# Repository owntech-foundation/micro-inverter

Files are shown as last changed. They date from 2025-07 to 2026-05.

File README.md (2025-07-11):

# An open-source - community built micro-inverter

## Manifesto 

The project goal are : 

- Having the first open source PV micro-inverter
- Finally a design easy to repair that is no longer a black box
- Redeem your data sovereignty, you will no longer depend on a proprietary cloud to follow your solar production and consumption. 

## Open, for everyone, forever

- This project is propulsed by its community. 
- The collective work generated is meant to remain open.
- Design files are made with open source software - Namely kiCAD.

In that sense, the owntech foundation aims at protecting this technical common.

## (ultra) Preliminary specifications

- 230V AC grid code compliant
- 450W max per module
- no invasive potting that prevents reparability

## Licence 

This project is licenced under **CERN-OHL-V2-S** open source hardware licence. Licence file can be found under `License/cern-ohl-v2-s`.

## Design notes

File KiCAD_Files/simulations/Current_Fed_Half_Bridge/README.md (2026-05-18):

# LTspice Current-Fed Half-Bridge Simulation

This directory contains an LTspice simulation for a current-fed half-bridge converter stage. The schematic models the MOSFET bridge drive, input current-feed network, transformer/coupled inductors, rectifier/output stage, and a TI UCC27282 half-bridge gate driver model.

## Files

- `Current_Fed_Half_Bridge.asc` - main LTspice schematic.
- `UCC27282.asy` - custom LTspice symbol for the UCC27282 gate driver.
- `ucc27282.lib` - TI transient SPICE model for the UCC27282.

## Simulation Setup

The schematic includes these simulation directives:

```spice
.param Tsw={1/Fsw} Ton={duty*Tsw} Toff={TSw-Ton-2*dt} dt=100n duty=0.45 Fsw=200k
.tran 0 0.002 0 0.000001
K1 L1 L2 1
```

Nominal operating parameters:

- Switching frequency: `Fsw = 200 kHz`
- Duty cycle: `duty = 0.45`
- Dead time: `dt = 100 ns`
- Transient duration: `2 ms`
- Maximum timestep: `1 us`
- Input source: `Vin = 40 V`
- Gate-drive supply: `VDD = 12 V`

## Main Circuit Elements

- `U1` - UCC27282 high/low-side gate driver.
- `M1`, `M2`, `M3` - `IPP048N12N3` MOSFETs.
- `L3` and `C7` - input current-feed/filter elements.
- `L1` and `L2` - coupled inductors/transformer winding pair.
- `D1`, `D2`, `C4`, `C6`, and `R9` - rectifier, output capacitance, and load.
- `V2`, `V3` - complementary gate-drive pulse sources for `LI` and `HI`.

## Running the Simulation

1. Open `Current_Fed_Half_Bridge.asc` in LTspice.
2. Keep `UCC27282.asy` and `ucc27282.lib` available in the same project directory, or install the symbol/model into your LTspice symbol and library search paths.
3. Run the transient simulation.
4. Probe the relevant nets listed below.

If LTspice cannot find the UCC27282 symbol, update the symbol reference in the schematic or copy `UCC27282.asy` into the expected LTspice symbol path. The schematic currently references the driver symbol as `lib\\JAL\\UCC27282`.

## Useful Probe Nodes

- `Vin` - converter input voltage.
- `LI`, `HI` - gate-driver logic inputs.
- `LO`, `HO` - low-side and high-side gate-driver outputs.
- `VSH` - high-side switch node.
- `VGSH` - measured high-side gate-to-source voltage.
- `VHigh` - high-side supply node.
- `Vout` - output voltage node.
- `GNDhigh` - output-side return.
- `VOUT_mes` - behavioral output voltage measurement, `V(Vout)-V(GNDhigh)`.
- `vr1` - behavioral measurement of `V(vsh)-V(vshcap)`.
- `vr2` - behavioral measurement of `V(vsecd)-V(vsecc)`.

## Notes

- The UCC27282 model is a TI PSPICE transient model released by Texas Instruments in 2018 and included here as `ucc27282.lib`.
- The schematic depends on LTspice device models for parts such as `IPP048N12N3`, `VS-E5TX1506`, and `VS-E5TH1506`. If those models are not available in your LTspice installation, add the required vendor libraries or replace the parts with available equivalents.
- The schematic uses micro-unit values that may appear as special characters in the raw `.asc` text. LTspice should display these values normally when the schematic is opened.

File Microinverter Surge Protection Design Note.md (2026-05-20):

Surge Protection for the OwnTech microinverter

Author: Stevie Wray – Fairflow Energy Ltd.

Date: 14/05/2026

Revision: V1.0

# Rationale – Why should there be surge protection?

The microinverter is intended to be connected directly to an AC grid.
This grid could have transient over voltages from lightning, grid
switching and inductive faults. These could exceed insulation limits and
cause immediate or long term damage to sensitive components. By
including surge protection, the more sensitive components can continue
to work in a wider range of circumstances.

There is also a regulatory element where withstanding surges are a
requirements for passing EMC tests.

The relevant standards for this are:

EN 62109-1: Safety of power converters for use in photovoltaic power
systems - Part 1: General requirements

EN 62109-2: Safety of power converters for use in photovoltaic power
systems - Part 2: Particular requirements for inverters

EN 61000-4-5: Electromagnetic compatibility (EMC) – Part 4-5: Testing
and measurement techniques – Surge immunity test

# What have we done?

1\. Included an AC side Metal Oxide Varistor (MOV) and Gas Discharge
Tube (GDT) combination to protect against line to earth surges. (Live or
Neutral counting as a line) – RV1, RV3, GD1

2\. Included an AC side MOV to protect against Live to Neutral surges. -
RV2

3\. Included a further set of line to earth and live to neutral MOVs on
the converter side of the K1 grid connection relay. This set of MOVs are
paired with fuses in case of protective device failure. – RV101, RV102,
RV103, F1, F101.

4\. Considered insulation co-ordination to ensure that insulation is
sufficient in each part of the inverter.

NOTE: If a protective device fails, the microinverter will need
maintenance to replace those components.

An excerpt of the microinverter schematic is included below showing
these MOVs.

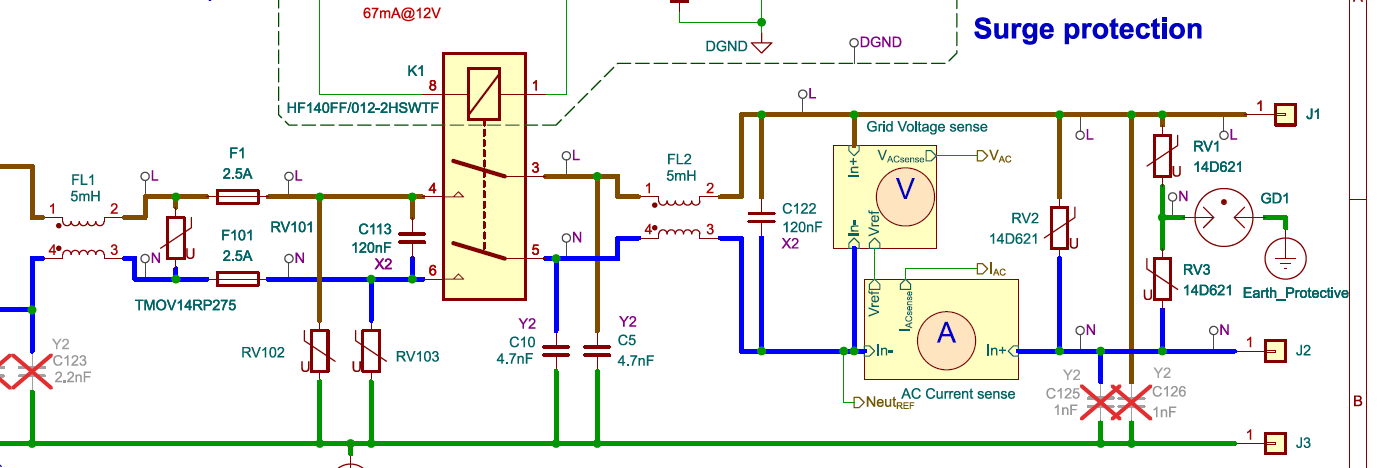
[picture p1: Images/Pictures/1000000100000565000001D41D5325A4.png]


## 

# Why have we done it that way?

On the specific device configuration, a major consideration is the
failure mode of the MOVs and the GDTs themselves. If the fault through a
GDT does not clear (reduce current to zero) then the GDT will eventually
catch fire. This is undesirable! As such, the arrangement for line to
earth fault with a MOV in series with a GDT overcomes this. Especially
if the MOV has an internal thermal fuse. The MOVs selected do have an
internal fuse.

There is also a cascade of MOV values starting with the higher values
near the AC connection to the grid, and reducing closer to the internals
of the inverter. The intent here is to ensure that sensitive components,
such as the GaN switches are protected to voltages that they can
withstand.

There is a known limitation with this current design, in that the rating
of the MOVs is still insufficient to reduce an arbitrary pulse to below
the voltage rating of the GaN switches. This is an unlikely event, as
the standard pulse simulated in this document are already a harsh
condition.

With this in mind, the intent is to meet EN61000-4-5 Surge Test Levels
as below, assuming that the AC power port is a class 4, but then
elements within the microinverter are then reduced in class.

This assumes that the standard tests are sufficient for a robust
product. From assessing them, they do seem good enough for the
microinverter’s purposes.

Essentially, the requirements we are aiming to meet are that after the
surge test (4 kV, 2 Ohm source impedance 8/20 µs pulse), the inverter
must:

- Continue to operate as intended (no degradation in performance).
- Not become unsafe (no fire, electric shock, or mechanical hazards).
- Not trip protective devices (e.g., circuit breakers) unless it is part
  of the intended safety function.

The defined voltage levels are found in this table here:

<table>
<tbody>
<tr>
<td colspan="4">Electrical Surge Test Levels (IEC/EN 61000-4-5)</td>
</tr>
<tr>
<td>Class</td>
<td>Test Level<br />
(V)</td>
<td>Max Peak Current @ 2 Ω<br />
(A)</td>
<td></td>
</tr>
<tr>
<td>1</td>
<td>500</td>
<td>250</td>
<td></td>
</tr>
<tr>
<td>2</td>
<td>1000</td>
<td>500</td>
<td></td>
</tr>
<tr>
<td>3</td>
<td>2000</td>
<td>1000</td>
<td></td>
</tr>
<tr>
<td>4</td>
<td>4000</td>
<td>2000</td>
<td></td>
</tr>
<tr>
<td>X</td>
<td>Special</td>
<td>Special</td>
<td></td>
</tr>
<tr>
<td colspan="3">X can be any level specified in product specific
standards.<br />
It can be above, below or between the others.</td>
<td></td>
</tr>
</tbody>
</table>

Wikipedia (<https://en.wikipedia.org/wiki/IEC_61000-4-5>)

Practically, the surge immunity testing is done with a combination
waveform generator, aiming to generate a 8/20 µs current pulse. Note the
waveform times refer to rise time and impulse width. Shown nicely in
this excerpt from the Brightking 621KN14 datasheet.

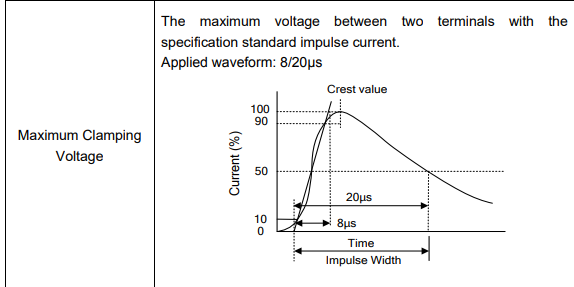
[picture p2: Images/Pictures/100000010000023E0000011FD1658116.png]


A combination waveform generator can be represented as a set of simple
circuit components, especially for simulation. The following is from a
guide found here:
<https://youspice.com/spice-simulation-of-a-combo-wave-generator/>

[](https://youspice.com/spice-simulation-of-a-combo-wave-generator/)

Cc=7.76μF, Rs1=14.8 Ohm, Rm=1.05 Ohm, Lr=9.74μH, Rs2=23.3 Ohm. The peak
voltage on Rs2 can be 1KV, 2KV,..6KV.

A SIMBA model has been produced with these parameters, pre-charging the
capacitor Cc to the desired voltage rating for the test. In this case it
is generally 4 kV.

# Simulations for verification

## RV1, RV2, RV3: Brightking 621KN14

The device selected for RV1, RV2 and RV3 is the Brightking 621KN14. The
section below shows the expected characteristics of this device, and
shows an example of it under a 4 kV, 2 Ohm input impedance surge
immunity test using a simulated combination wave generator.

Varistor voltage is the voltage
between two terminals with specified measuring current of 1mA DC.



~0 Amps at less than 620 V

~ 1 mA at 620 V

~ 50 A at 1025 V

~ 2 kA at 1800 V

R = dV / dI = (1800-620) / (2000 – 0.001) = 0.59 Ohms

620 V breakdown voltage, 0.59 Ohm breakdown resistance, 0 Ohm on
resistance. Back to back configuration.

Validated in simulation as a “good enough” model with the combination
wave generator.

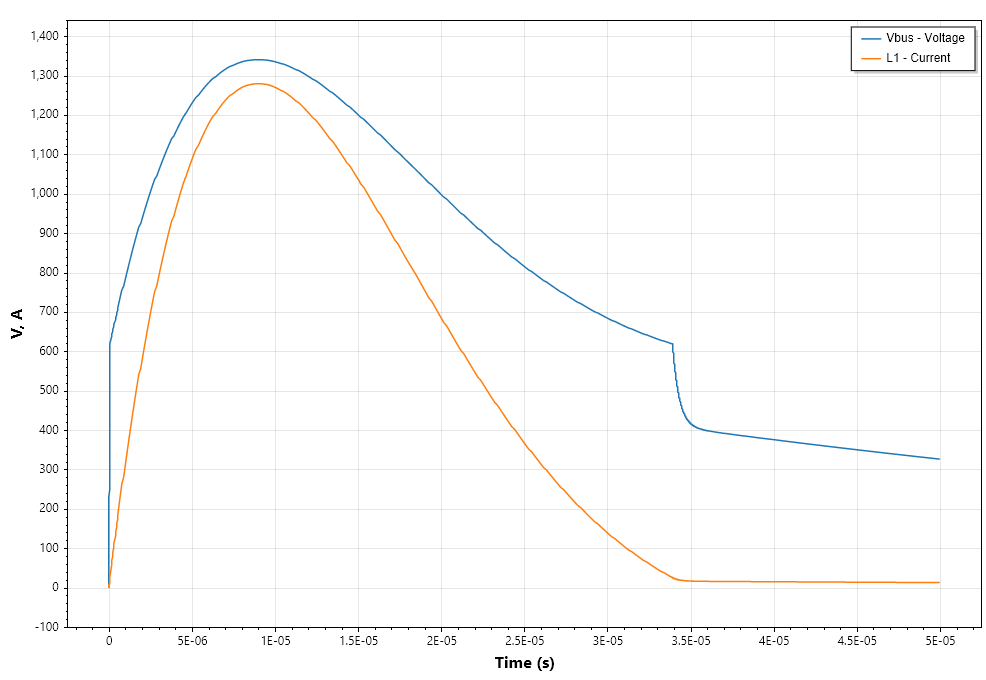
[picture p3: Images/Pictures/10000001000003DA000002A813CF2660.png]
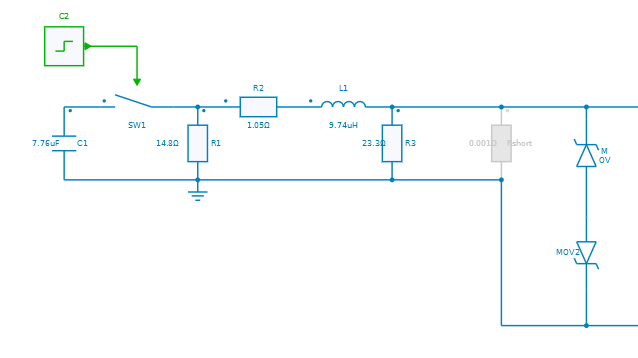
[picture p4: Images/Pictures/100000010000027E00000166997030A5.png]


## RV101, RV102, RV103: Littelfuse TMOV14RP275E

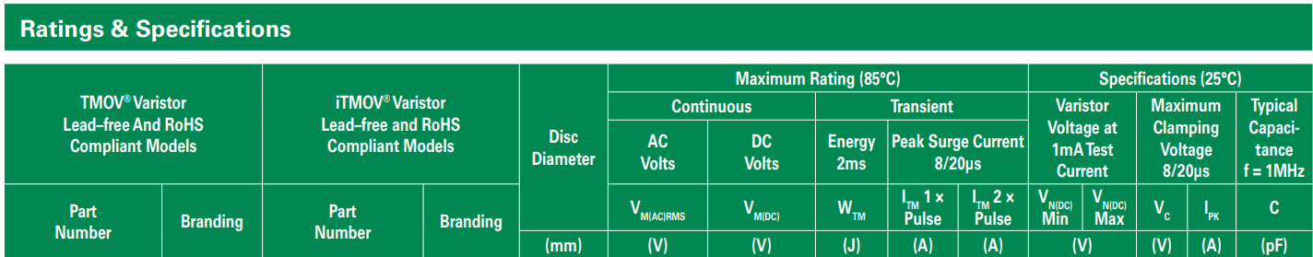
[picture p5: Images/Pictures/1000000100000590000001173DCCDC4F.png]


~0 Amps at less than 473 V

~ 1 mA at 473 V

~ 50 A at 710 V

~ 2 kA at 1000 V

R = dV / dI = (1000-473) / (2000 – 0.001) = 0.26 Ohms

473 V breakdown voltage, 0.26 Ohm breakdown resistance, 0 Ohm on
resistance. Back to back configuration.

Validated in simulation as a “good enough” model with the combination
wave generator.

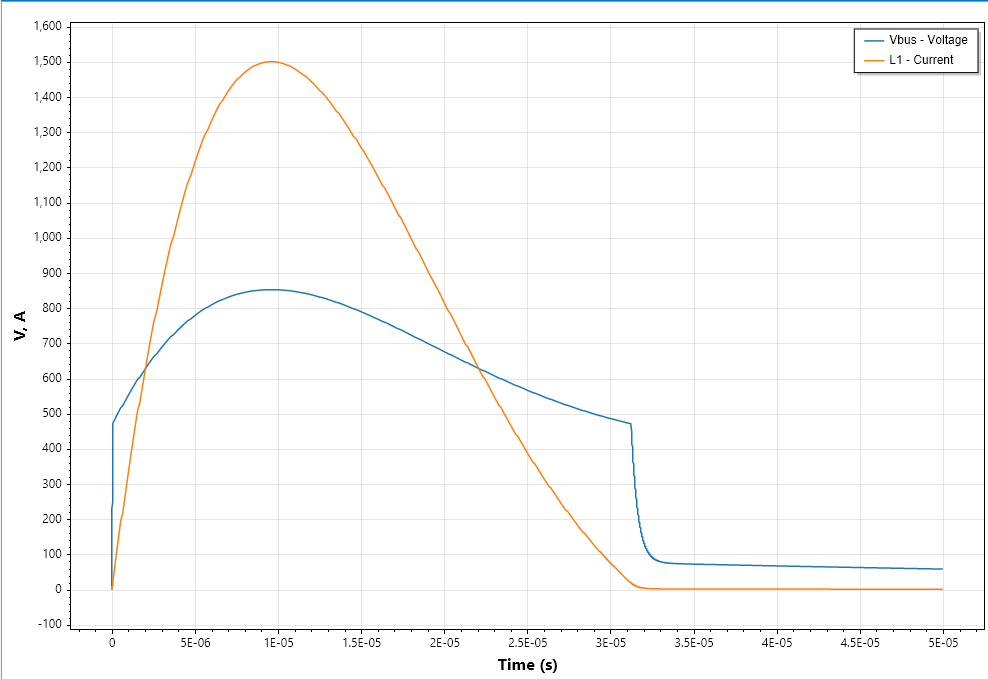
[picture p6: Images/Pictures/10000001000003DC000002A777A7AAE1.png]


## GD1: RUILON 2R600B-8S

The device selected for GD1 is the RUILON 2R600B-8S. The section below
shows the expected characteristics of this device, and shows an example
of it under a 4 kV, 2 Ohm input impedance surge immunity test using a
simulated combination wave generator.

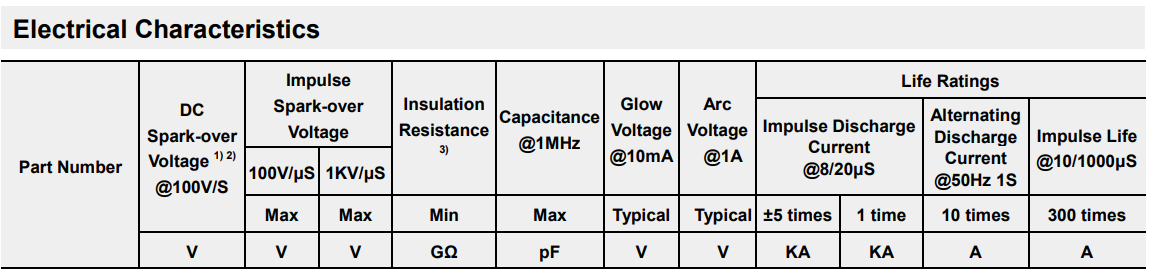
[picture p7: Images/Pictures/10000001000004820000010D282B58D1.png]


R = V / I = 15 / 1 = 15 Ohm at “Arc”

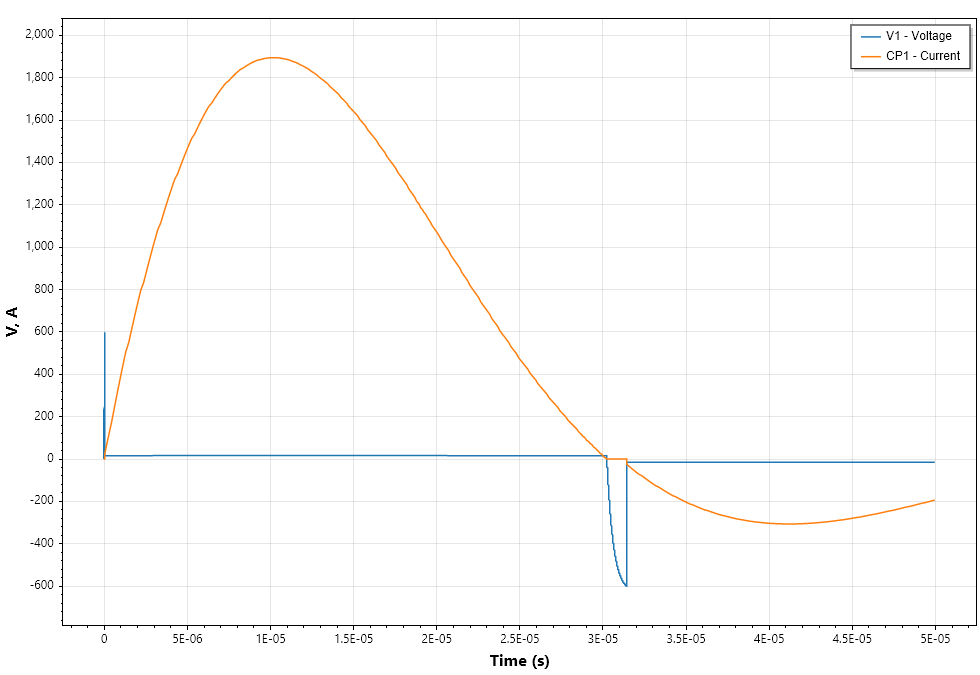
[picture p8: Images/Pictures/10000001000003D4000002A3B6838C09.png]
The simulation top level (left)
and the internals of the Gas Discharge sub circuit (right)

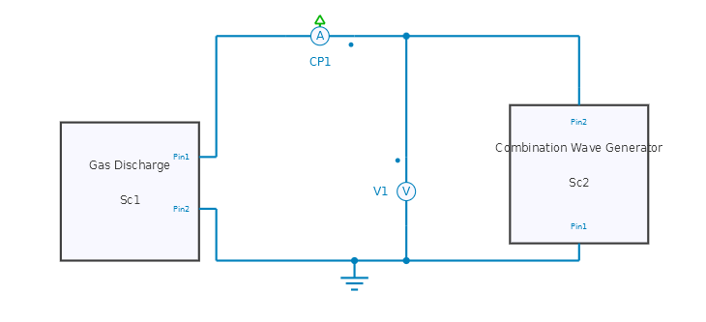
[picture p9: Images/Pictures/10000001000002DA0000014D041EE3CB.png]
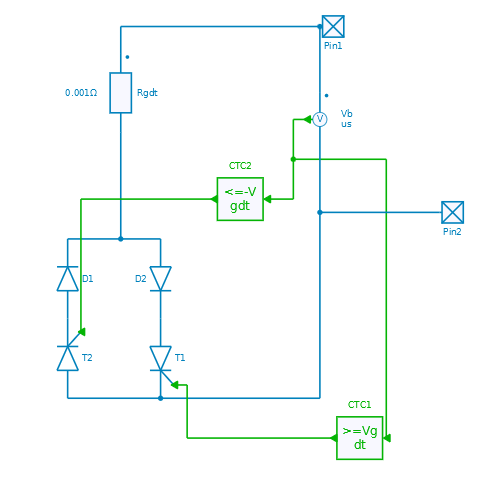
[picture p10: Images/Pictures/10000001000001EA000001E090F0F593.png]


Vgdt = 600 V, Vpeak = 4000 V

The GDT model is a thyristor with simple threshold control. There are
two thyristors in anti-parallel for bidirectional operation. Each
thyristor has a diode with a voltage drop of 15 V in series to represent
the plasma voltage of the GDT. There is also a low resistance element
(0.001 Ohm) to consider parasitics at the simplest level.

## Whole AC surge protection model

Whole AC end simulation with a 4 kV, 2 Ohm source impulse test from the
combination wave generator.

This is a line to earth fault scenario with surge voltage and current on
the top plot and capacitor voltages in distance-from-grid order on the
bottom plot.

It can be seen that the ~1350 V seen at the AC connections is reduced to
~650 V peak at C122, and reduced further through C113, C120 and the DC
link capacitor C6 sees virtually no change. There is significant ringing
due to the capacitive and inductive components interacting with each
other, but it is damped to zero within 50 ms.

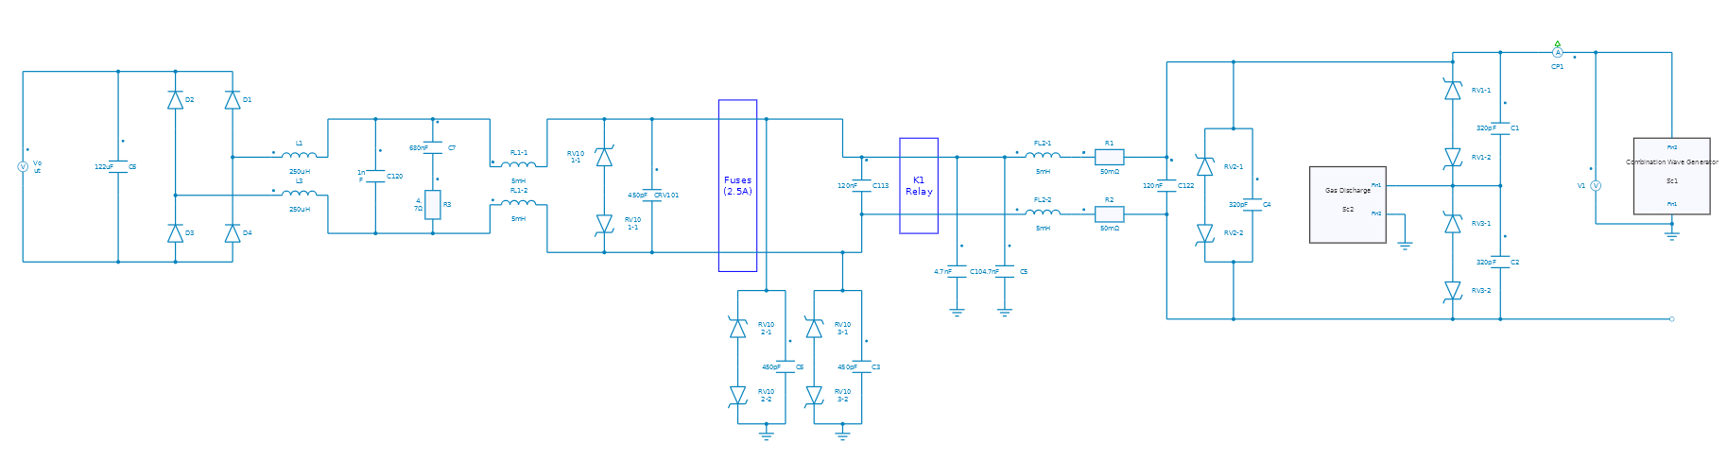
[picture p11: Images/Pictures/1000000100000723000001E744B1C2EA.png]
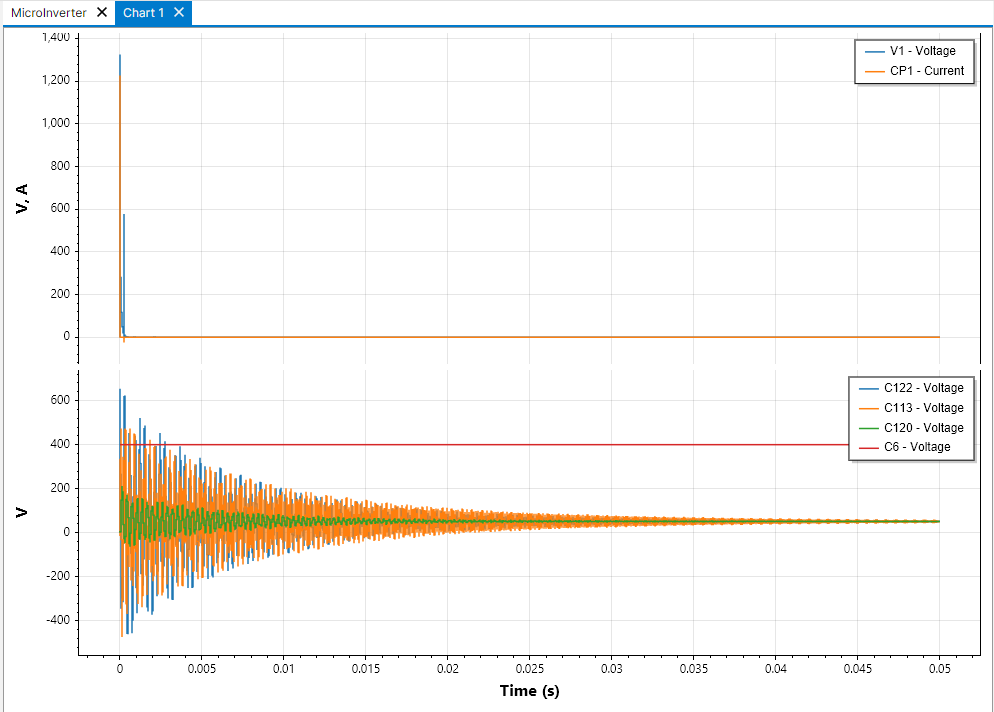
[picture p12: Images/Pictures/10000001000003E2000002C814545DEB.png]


This is a live to neutral surge test with the same plots as above.

It can be seen that the ~1350 V seen at the AC connections is seen in
its entirety by C122, but then subsequent capacitors C113 and C120 never
see a voltage above ~500 V. There is some ringing, but less in this
scenario and it is damped by approximately 20 ms. C6 is largely
unaffected by the surge.

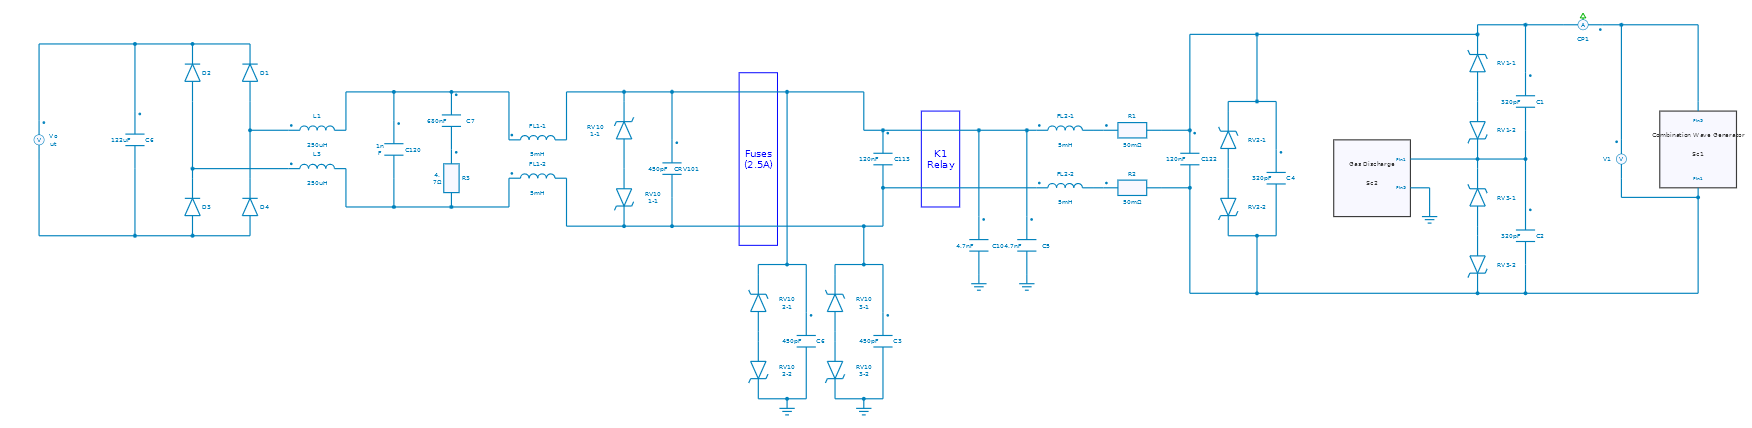
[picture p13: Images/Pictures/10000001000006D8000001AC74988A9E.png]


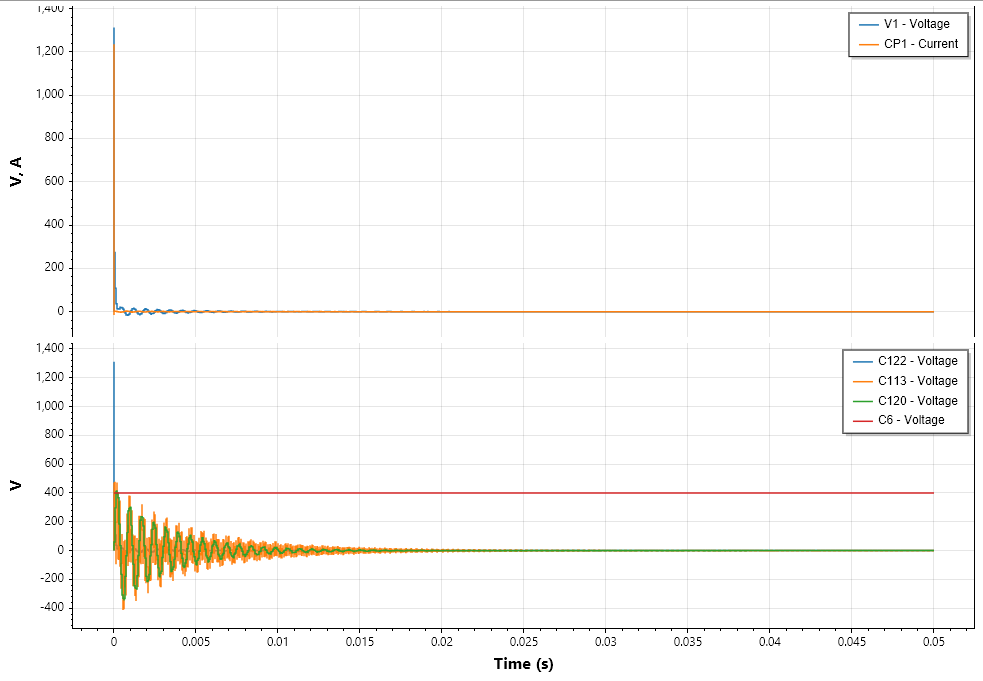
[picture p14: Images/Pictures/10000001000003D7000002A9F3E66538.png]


# 

# 

# Appendix: EN/IEC 61000-4-5 Excerpt

7.5.1 – Impulse voltage test (type test) The impulse voltage test is
performed with a voltage having a 1.2/50 µs waveform; see Figure 6 of
IEC 60060-1. It is intended to simulate overvoltages caused by lightning
or by the switching of equipment. See Table 15 for further details on
the impulse voltage test conditions. Tests on clearances smaller than
those required by Table 13, as permitted by 7.3.7.4.2, and tests on
solid insulation are performed as type tests using the appropriate
voltages from Table 16. Tests relating to the protective separation of
components and devices are performed as a type test before their
assembly into the PCE, unless the test can be performed on the complete
PCE without reducing the stress applied to the protective separation.
The test is performed using the impulse withstand voltages listed in
column 3 or 5 of Table 16.

Where transient limiting devices are used to reduce the impulse voltage
levels, see 7.3.7.1.2, item g), the reduction is verified by a type
test. The values from column 2 or 4 of Table 16 are applied to the PCE,
and measurements are taken in the circuit after the transient limiting
devices, in order to determine the reduced transient level. If it is
necessary to test a clearance designed for altitudes between 2 000 m and
20 000 m, using Table A.2 of IEC 60664-1, the appropriate test voltage
may be determined from the clearance by using Table 13 in reverse.

Table 15 — Impulse voltage test

|  |  |
|----|----|
| Subject | Test conditions |
| Test reference | Clause 19, paragraph 20.1.1 and Figure 6 of IEC 60060-1; 6.1.2.2.1 of IEC 60664-1 |
| Requirement reference | In accordance with 7.3.4.3, 7.3.5.3 and 7.3.7 |
| Pre-conditioning | Live parts belonging to the same circuit shall be connected together. Protective impedances shall be disconnected unless they need to be tested. The impulse voltage shall be applied: 1) between the circuit under test and its environment, and 2) between the circuits to be tested. Power is not applied to the circuits under test. |
| Initial measurement | In accordance with the specification of the PCE, component or device. |
| Test equipment | 1.2/50 µs impulse generator with an effective internal impedance of less than 2 Ω for clearance tests and 500 Ω for component and solid insulation tests. |

|  |  |  |
|----|----|----|
| Subject | a\) | b\) |
| Measurement and verification | Clearances smaller than those required by Table 7. Clearances reduced by transient limiting devices or by circuit characteristics. Solid basic or supplementary insulation. | Solid reinforced insulation. Clearances, components and protective separation devices. Three 1.2/50 µs impulses of each polarity at intervals ≥ 1 s, with peak voltage ±5% in accordance with: |
| Test voltage | Column 2 or 4 of Table 16. | Column 3 or 5 of Table 16. |
| Test voltage note | When the test is performed on a clearance at an altitude below 2 000 m, the test voltage shall be increased in accordance with Table F.5 of IEC 60664-1, reproduced as Table F.2 in this International Standard. | Same condition applies. |

Table 16 — Impulse withstand test voltage

|  |  |  |  |  |
|----|----|----|----|----|
| System voltage (see 7.3.7.2.1) | Insulation between circuits **not directly connected to the mains** and their environment, according to **overvoltage category II** — Basic or supplementary | Insulation between circuits **not directly connected to the mains** and their environment, according to **overvoltage category II** — Reinforced | Insulation between circuits **directly connected to the mains** and their environment, according to **overvoltage category III** — Basic or supplementary | Insulation between circuits **directly connected to the mains** and their environment, according to **overvoltage category III** — Reinforced |
| V | V | V | V | V |
| ≤ 50 | 500 | 800 | 800 | 1 500 |
| 100 | 800 | 1 500 | 1 500 | 2 500 |
| 150 | 1 500 | 2 500 | 2 500 | 4 000 |
| 300 | 2 500 | 4 000 | 4 000 | 6 000 |
| 600 | 4 000 | 6 000 | 6 000 | 8 000 |
| 1 000 | 6 000 | 8 000 | 8 000 | 12 000 |
| — | Interpolation permitted | Interpolation permitted | Interpolation prohibited | Interpolation prohibited |

**Note for columns 2 and 3:** Test voltages for overvoltage categories I
and III may be derived in a similar way from Table 12.

**Note for columns 4 and 5:** Test voltages for overvoltage categories
II and IV may be derived in a similar way from Table 12.

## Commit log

2024-06-20 Initial commit Dual Active Bridge.
    [DAB.kicad_sch, Driver.kicad_sch, Driver_High.kicad_sch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]
2025-07-11 Initial commit micro-inverter
    [DAB.kicad_sch, Driver.kicad_sch, Driver_High.kicad_sch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]
2025-07-11 Change the repo structure to match standard tree.
    [Driver.kicad_sch, Driver_High.kicad_sch, Flyback.kicad_sch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]
2026-05-18 Adding a LTSpice simulation for the DCDC current fed half bridge. (#42)
